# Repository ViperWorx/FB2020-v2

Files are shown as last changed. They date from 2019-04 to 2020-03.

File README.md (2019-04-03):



This is a complete re-work of our [FB2020 CoreXY](https://github.com/AxMod3DPrint/FB2020) design that fixes any faults that we have noticed over the 3 years we have had these in service in our farm. 

The Changes are listed below, this is by no means a full changelog, but the main changes are listed below:-

Major Changes v2
-----------------

* Belt Alignment - Belts were not in line, motors moved to back of printer.
* All parts redesigned or re-modelled  
* XY Gantry now underslung, due to this Z height is reduced to 120mm. This may change in a future iteration.
* Now Clad on three sides with 3mm Acrylic (Perspex). 
* Electronics now changed to MKS Gen L
* Heated bed changed to Mains Voltage heater and Aluminum Plate
* Due to the above 2 Solid State relays are needed one for PS_ON (optional) and one for the Bed (Manditory)
* Bed Long extrusions changed to 220mm to centralise the bed.
* Bed now has an 6mm Acyrilic or 2mm Aluminum (preferred) laser cut base plate to improve stability and improve ease of levelling.
* Due to the above Z Axis Bed mounting printed parts have had the levelling removed. 
* Z Lead Screw alignment fixed
* Alignment printed tools for Y & Z added. (Can be permanently mounted)
* PEI now recommended build surface. 
* Recommended firmware is now [Klipper](https://github.com/KevinOConnor/klipper)

Reliability, Speed, Accuracy, Open Source
-----------------------------------------

This sums up the FB2020 CoreXY 3D Printer. We use these printers ourselves and wouldn’t sell the kits if we didn’t think they were up to snuff. Our FB2020s have run thousands of hours with very little down time. We print all the FB2020 printed parts on our FB2020s.

Speed & Reliability
-------------------

The FB2020’s heart is the MKS GEN L running the Klipper Firmware. Klipper runs from a Raspberry Pi and offloads all calculations to the Pi. This means the FB2020 is even faster than the v1. It has tried and trusted A4988 Stepper Drivers moving the motors, which can be upgraded to Trinamic TMC 2130 for super quiet operation. With an AxMod 3D Print Drakon Geared extruder powering the filament through the bowden tube into a Genuine E3D v6 Hot end. This makes for a winning combination. The heated bed is a mains voltage heater bonded to Tool Grade 5mm Aluminium Plate which means you can print any material you wan.

Low Maintenance Accuracy
------------------------

Running the E3D v6 and the Drakon Geared Extruder, it’s smooth printing. The FB2020 is capable of layer heights of 60 Microns up to 500 Microns and can print pretty much any filament you can throw at it. 

The Bill of Materials and further infomation can be found in the Wiki.

---

<table border="0px">
<th align="left">
&copy; AxMod 3D Print 2019.
</th>
<tr>
<td>
This documentation describes Open Hardware and is licensed under the CERN OHL v. 1.2.
</td>
</tr>
<tr>
<td>
You may redistribute and modify this documentation under the terms of the
CERN OHL v.1.2. (http://ohwr.org/cernohl). This documentation is distributed
WITHOUT ANY EXPRESS OR IMPLIED WARRANTY, INCLUDING OF
MERCHANTABILITY, SATISFACTORY QUALITY AND FITNESS FOR A
PARTICULAR PURPOSE. Please see the CERN OHL v.1.2 for applicable
conditions
</td>

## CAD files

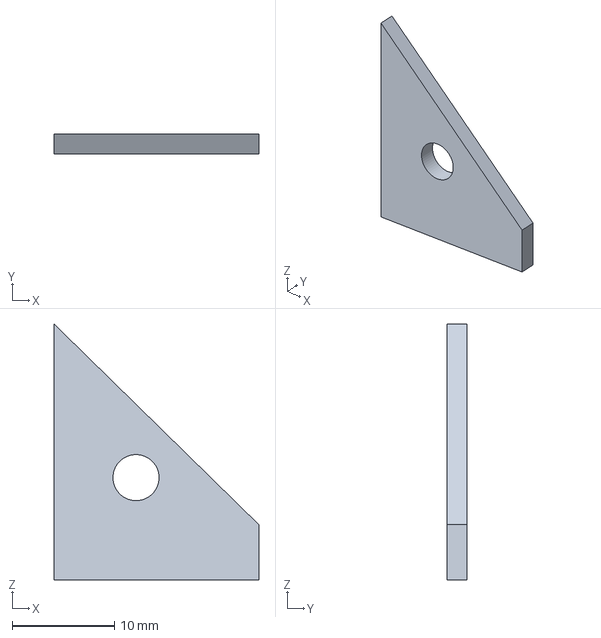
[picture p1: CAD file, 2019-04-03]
Alignment Tools/Y Alignment Tool Front.stp
20.0 x 2.00 x 25.0 mm

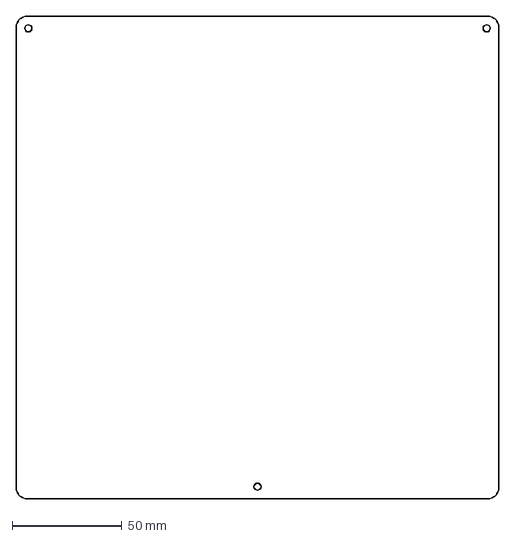
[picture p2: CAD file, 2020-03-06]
DXF/1 no Bed Plate.dxf
220.0 x 220.0 mm

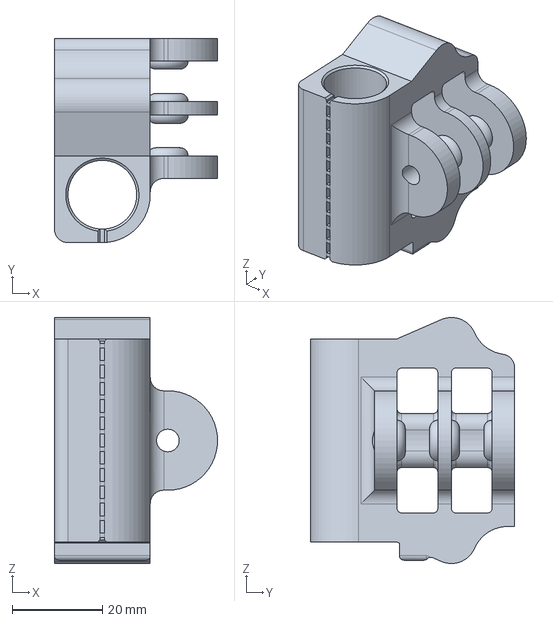
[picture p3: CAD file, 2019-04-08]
STEP/Y Carrier.stp
36.1 x 45.2 x 54.4 mm

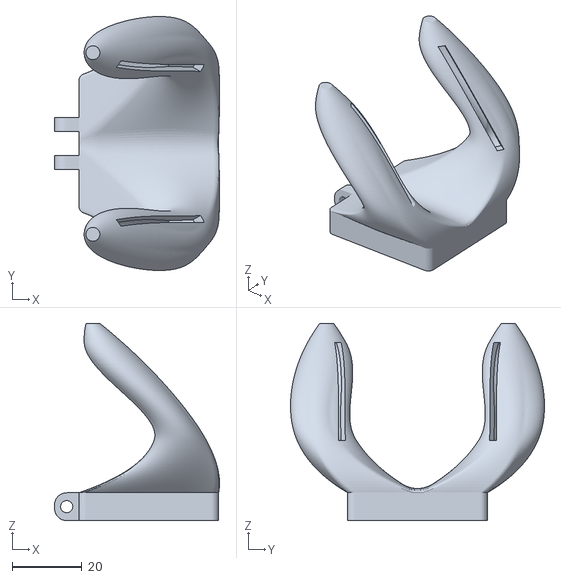
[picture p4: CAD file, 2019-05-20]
STL/1no Layer Fan Duct.stl
47.3 x 72.7 x 56.5

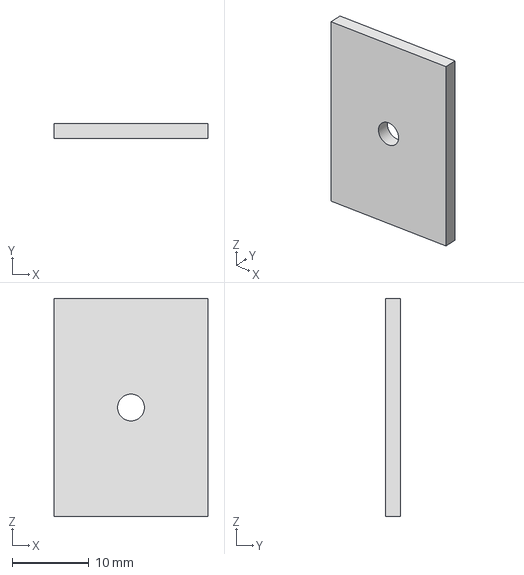
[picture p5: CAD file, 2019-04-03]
Alignment Tools/Y Alignment Tool Back.stp
20.0 x 2.00 x 28.4 mm

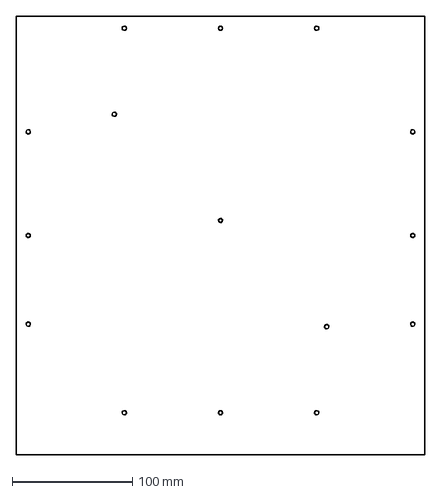
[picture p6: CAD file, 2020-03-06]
DXF/1no Side.dxf
340.0 x 365.0 mm

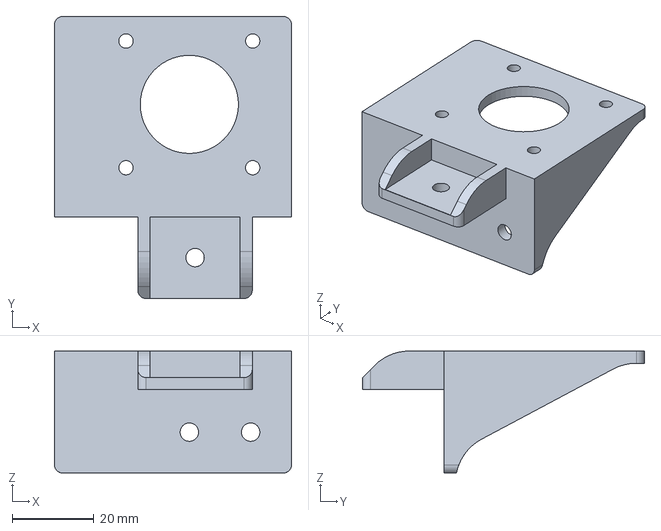
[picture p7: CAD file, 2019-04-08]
STEP/Motor Bracket Right.stp
58.0 x 69.0 x 29.9 mm

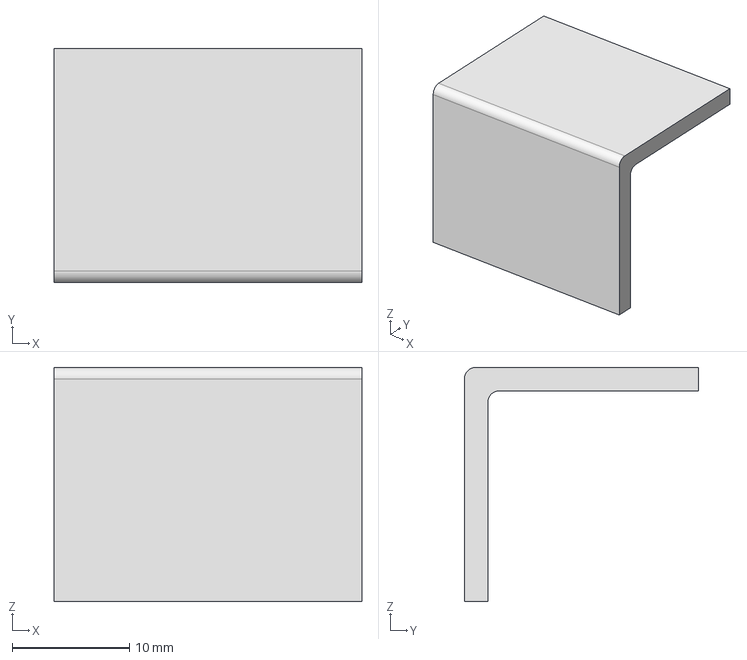
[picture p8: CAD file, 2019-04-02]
Alignment Tools/Z Motor Spacer Bottom.stp
26.3 x 20.0 x 20.0 mm

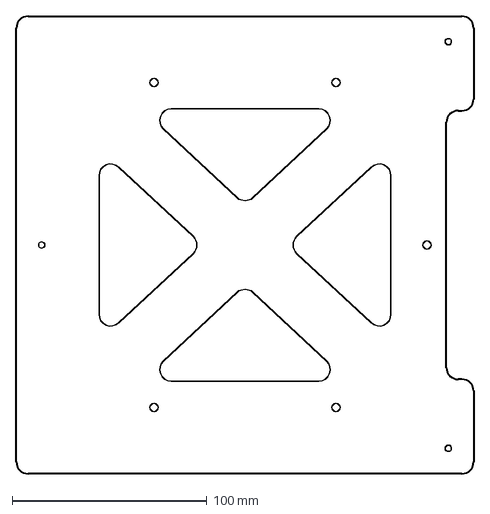
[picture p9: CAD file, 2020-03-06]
DXF/1no Bed Base Plate.dxf
235.0 x 235.0 mm

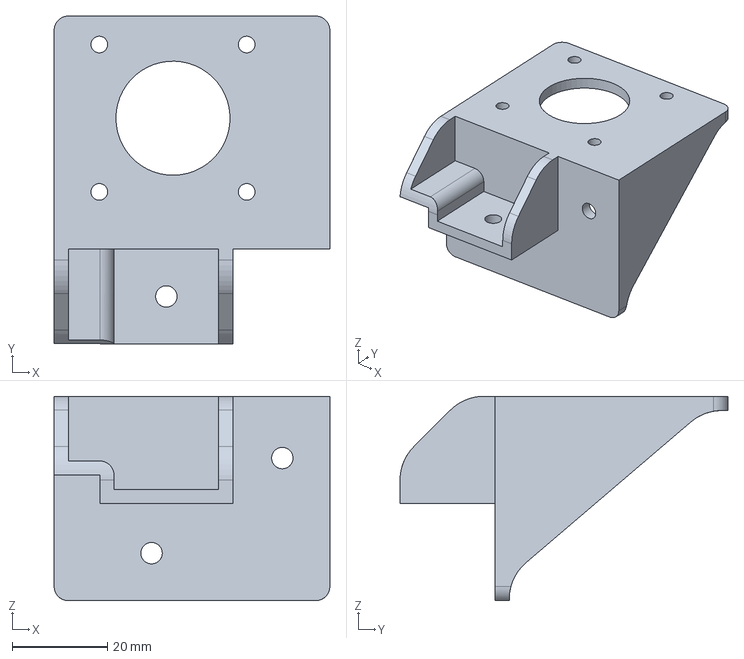
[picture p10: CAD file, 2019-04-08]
STEP/Motor Bracket Left.stp
58.0 x 69.0 x 43.0 mm

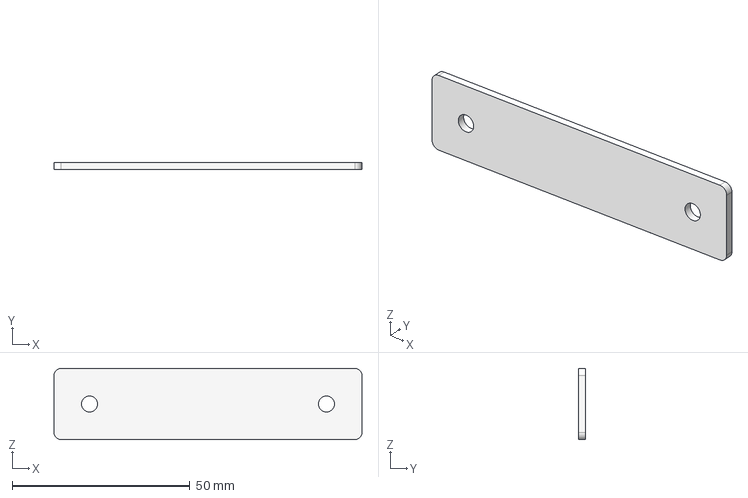
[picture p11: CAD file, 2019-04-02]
Alignment Tools/Z Axis Spacer.stp
86.7 x 2.00 x 20.0 mm

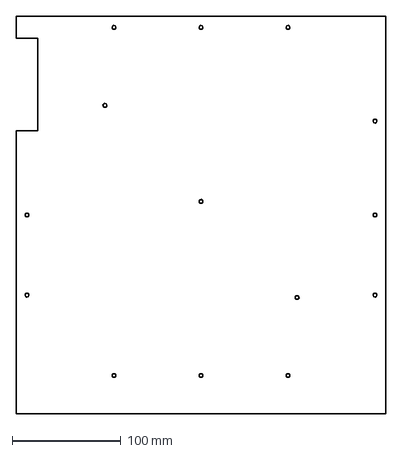
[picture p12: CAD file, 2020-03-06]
DXF/1no Side Cut - Extruder.dxf
340.0 x 365.0 mm

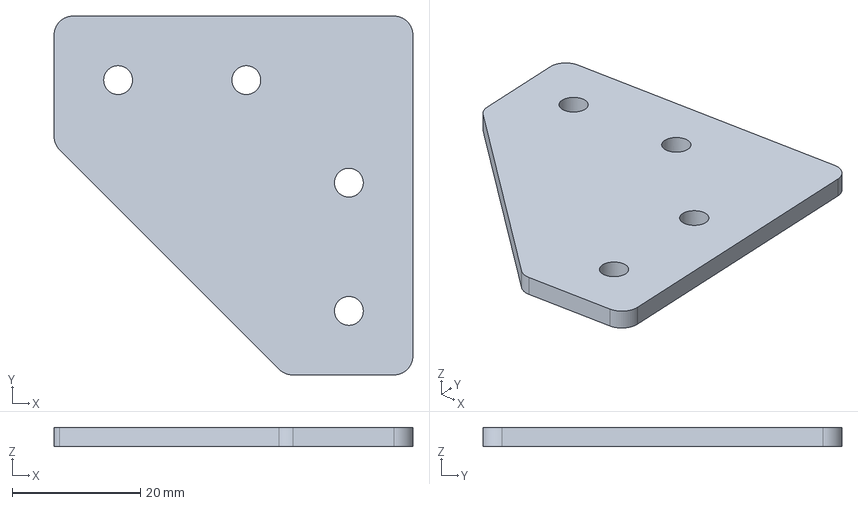
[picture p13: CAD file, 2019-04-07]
STEP/Front Top Corner Bracket.stp
56.0 x 56.0 x 3.00 mm

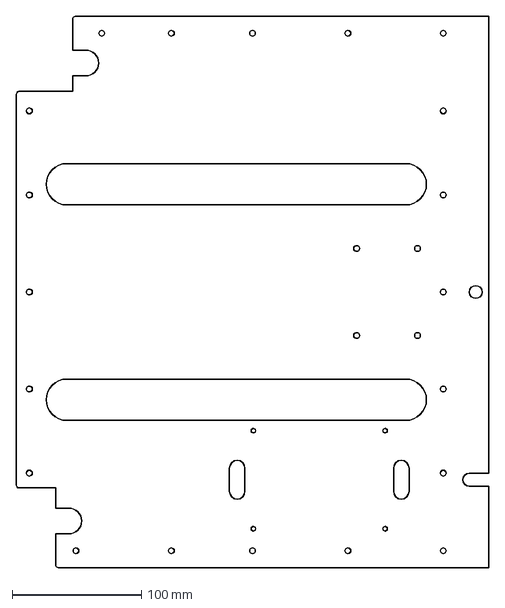
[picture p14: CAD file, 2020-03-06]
DXF/1no Back Acrylic.dxf
365.0 x 426.0 mm

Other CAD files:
STL/2no Y Carrier.stl
STL/1no Motor Bracket Right.stl
STL/1no Motor Bracket Left.stl
Alignment Tools/Z Axis Spacer Bottom.stl
Alignment Tools/Y Alignment Tool Back.stl
Alignment Tools/Y Alignment Tool Front.stl
Alignment Tools/Z Motor Spacer Bottom.stl
STEP/1no Z Motor Holder.stp
STEP/Bed Carrier Left.stp
STEP/Bed Carrier Right.stp
STEP/Carriage.stp
STEP/Corner Brace.stp
STEP/Corner Bracket.stp
STEP/Front Corner Bracket.stp
STEP/Idler Left.stp
STEP/Idler Right.stp
STEP/Layer Fan Duct.stp
STEP/Spool Holder.stp
STEP/Y Endstop Holder.stp
STEP/Y Rod Holder v2.stp
STEP/Z Endstop Mount.stp
STEP/Z Leadscrew Nut Mount.stp
STEP/Z Rod Holder.stp
STL/10no Corner Bracket.stl
STL/1no Bed Carrier Left.stl
STL/1no Bed Carrier Right.stl
STL/1no Carriage Clamp.stl
STL/1no Carriage.stl
STL/1no Idler Left.stl
STL/1no Idler Right.stl
STL/1no RRD Case Back.stl
STL/1no RRD Case Button.stl
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

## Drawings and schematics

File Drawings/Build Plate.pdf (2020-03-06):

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

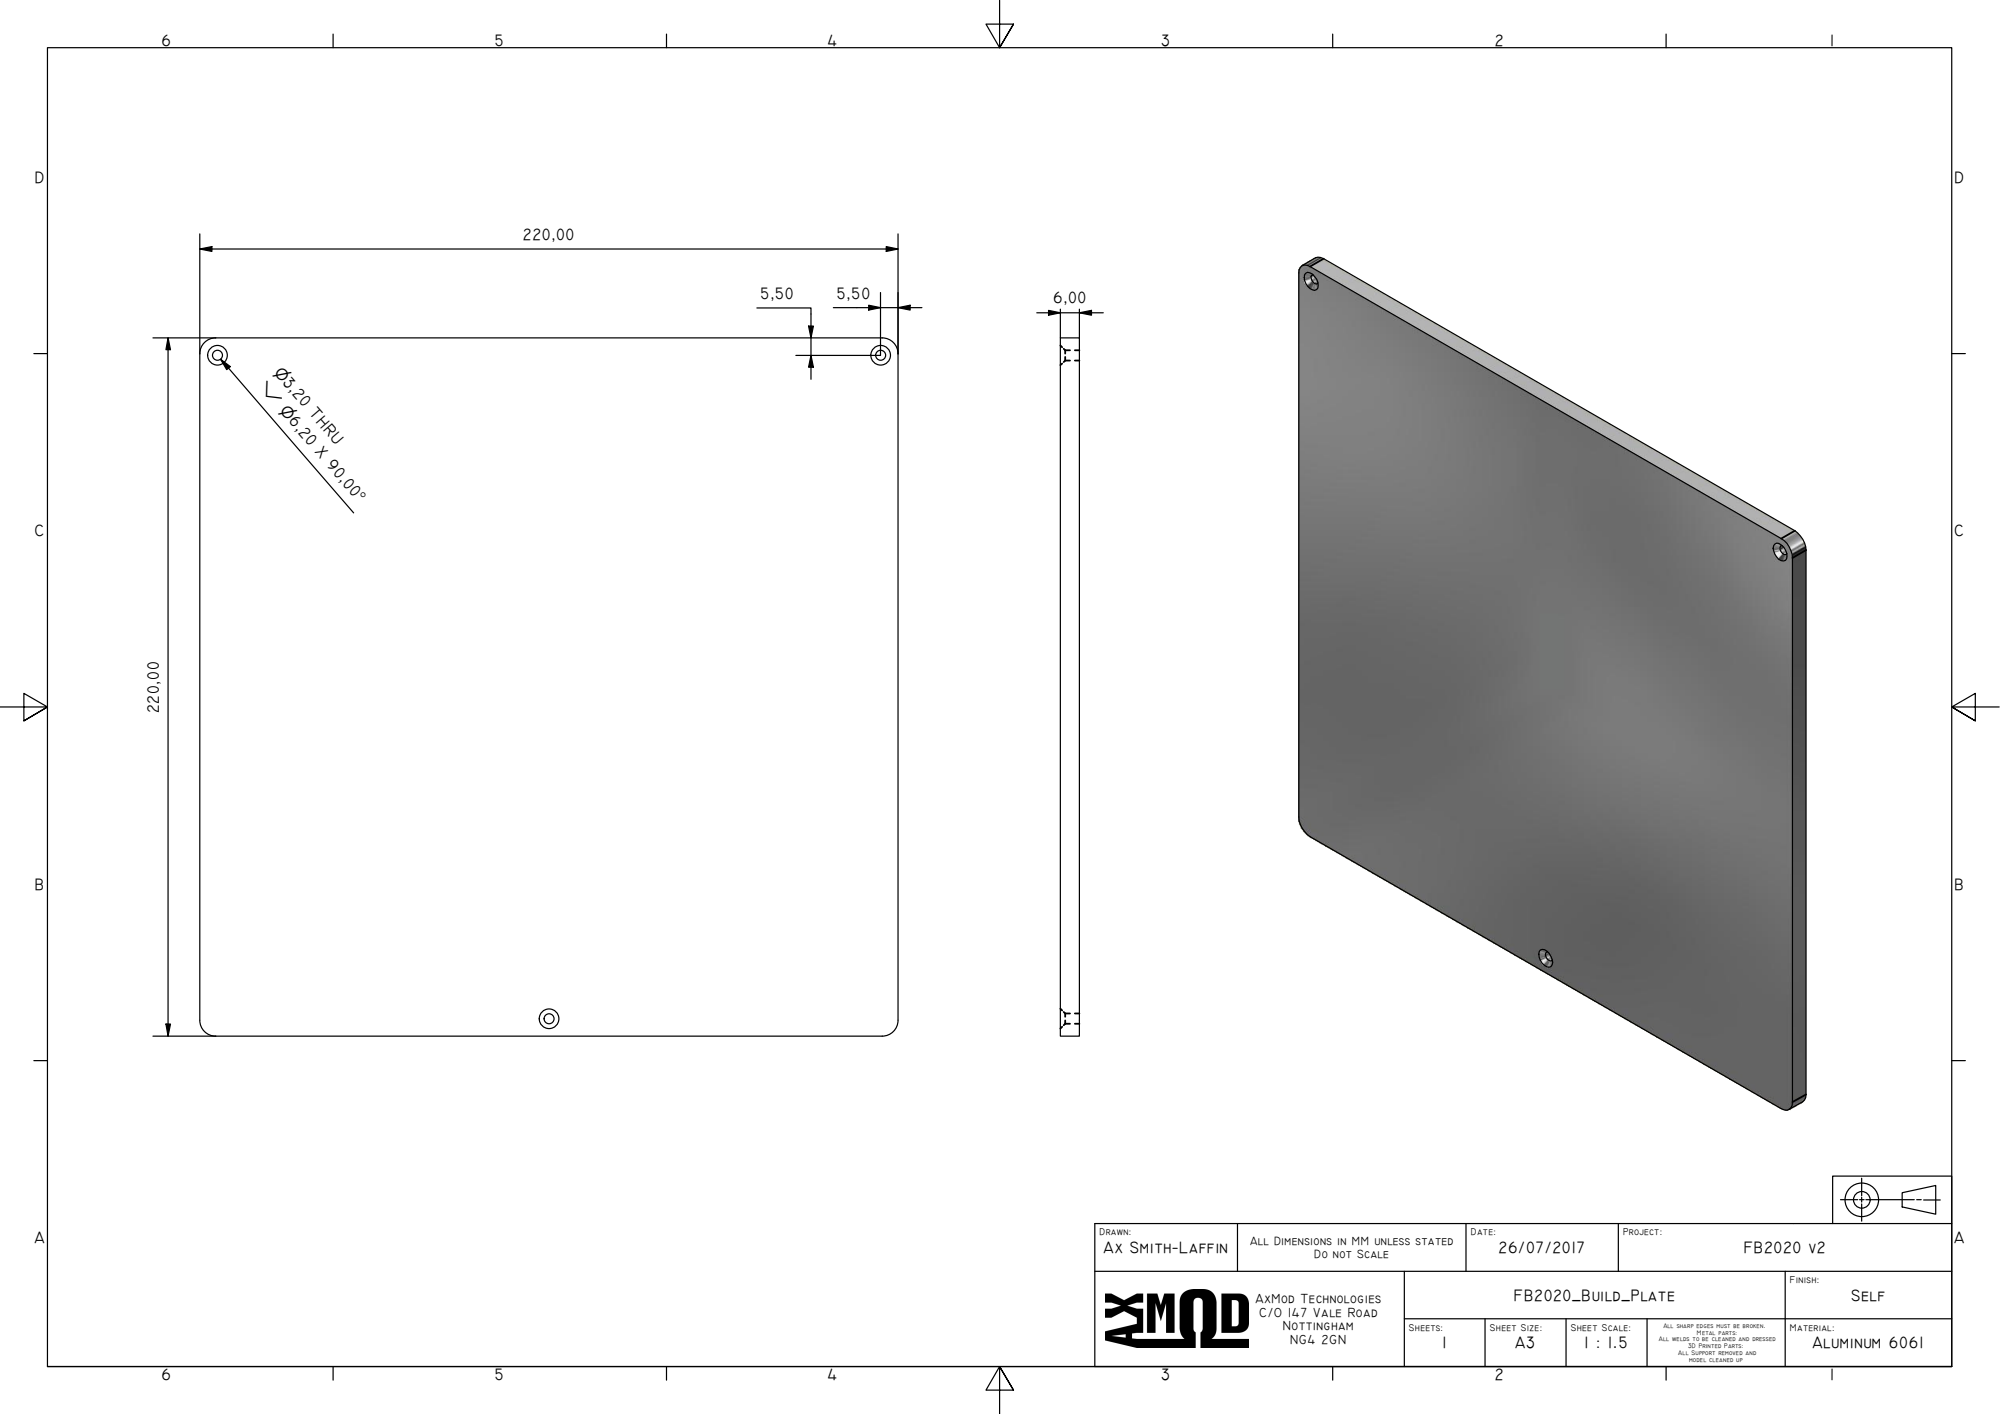
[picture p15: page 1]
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

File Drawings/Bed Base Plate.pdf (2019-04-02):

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

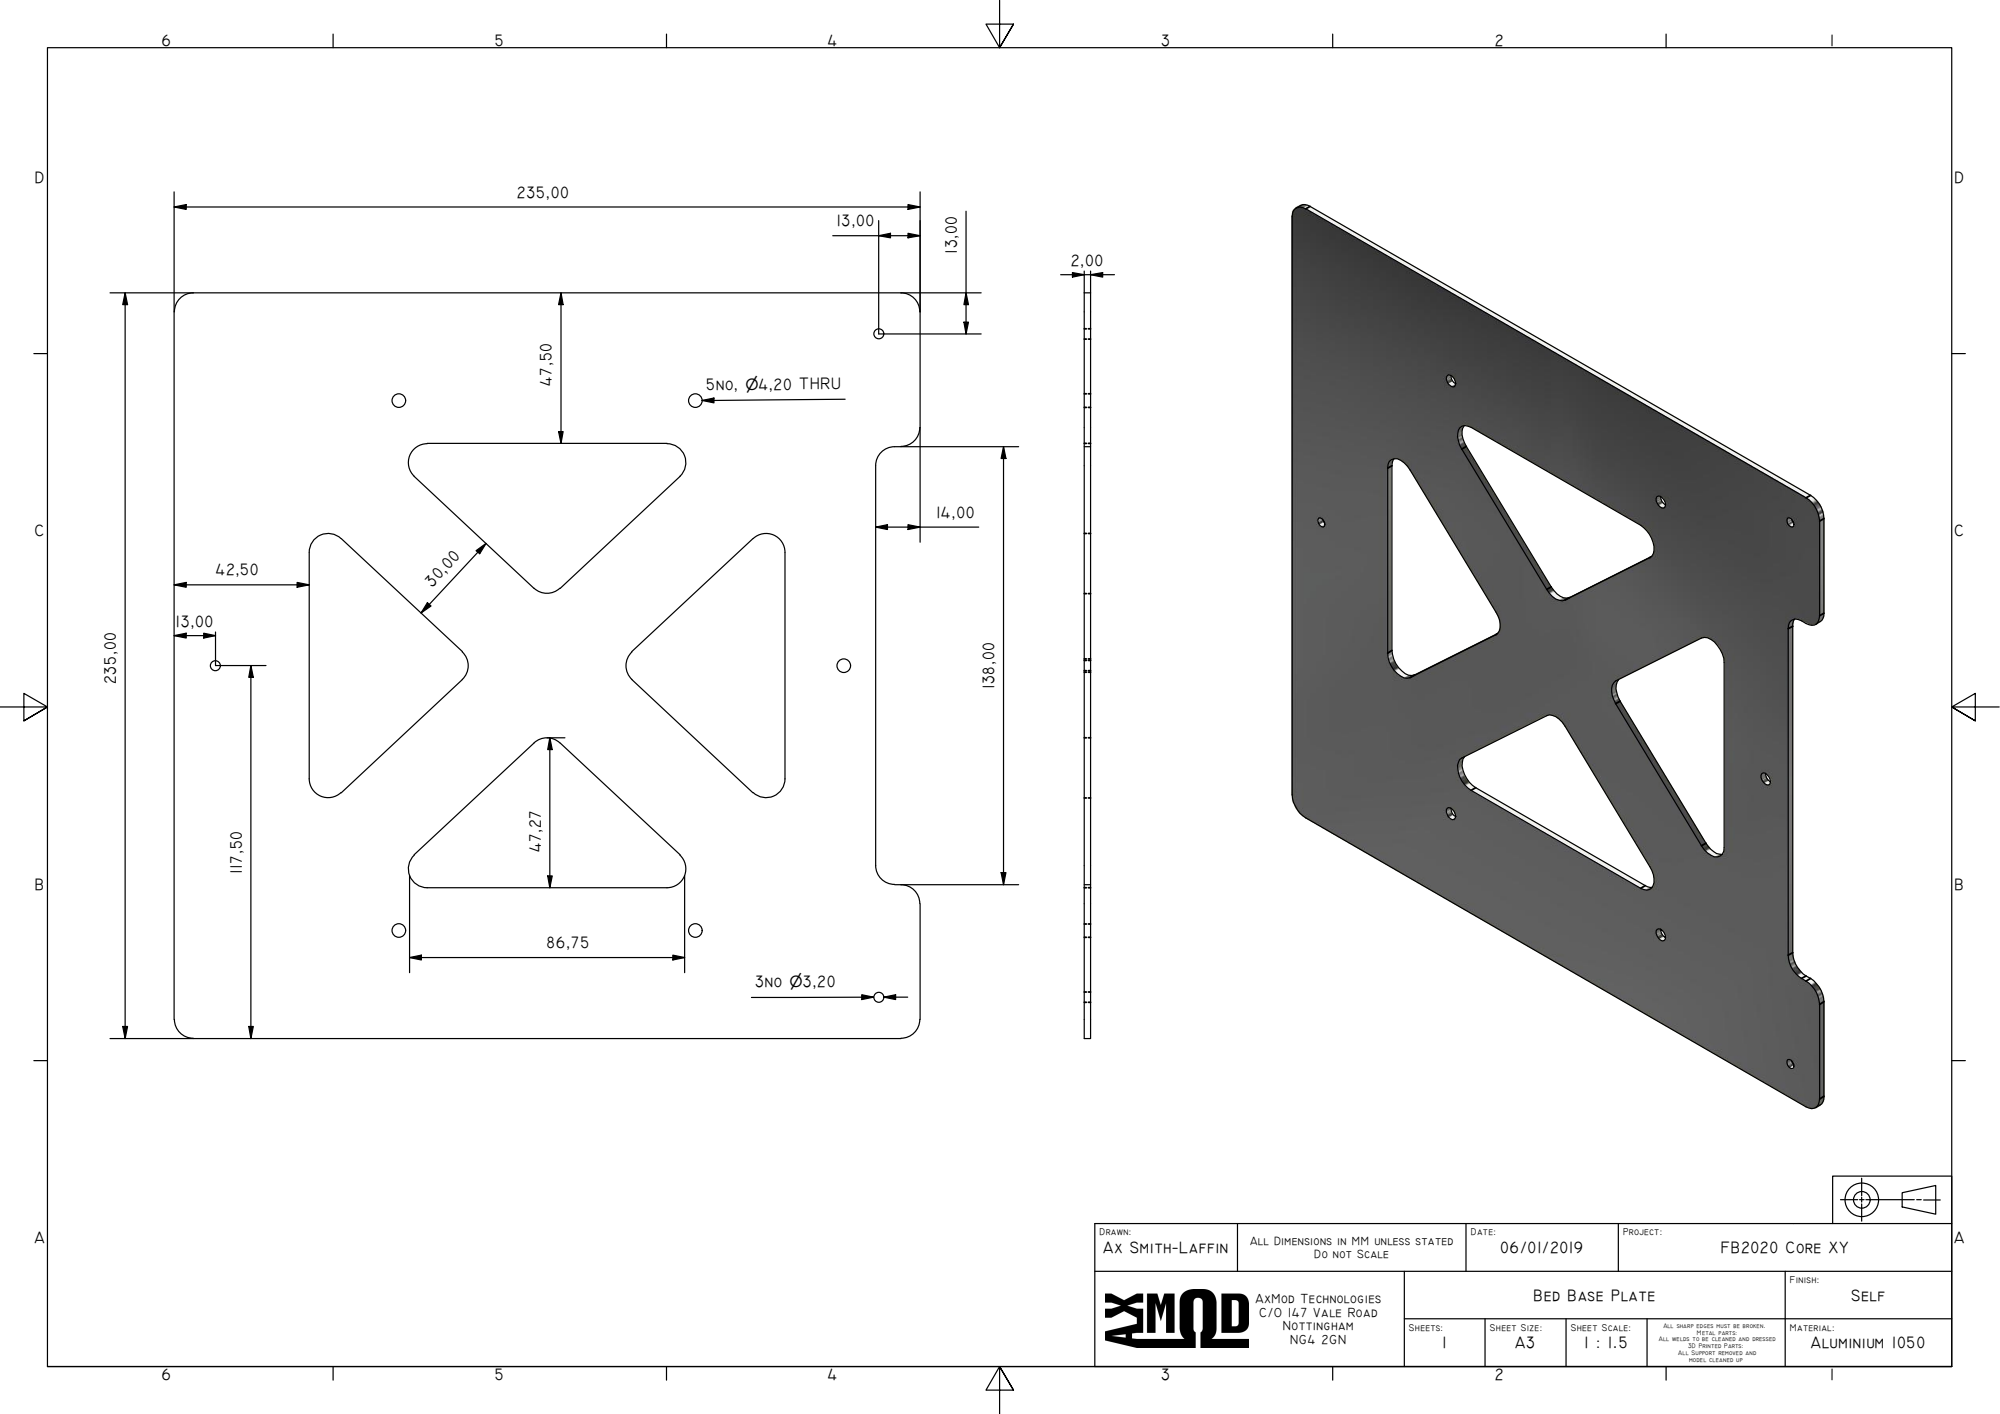
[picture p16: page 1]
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

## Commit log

2019-04-02 Initial Commit of Files
    [1 no Bed Plate.dxf, 1 no Motor Bracket Right.stl, 10no Corner Bracket.stl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]
2019-04-02 Move file to correct folder
    [4no Corner Brace.stl]
2019-04-03 Add Layer Fan Duct - Missed in initial commit
    [1no Layer Fan Duct.stl, Layer Fan Duct.stp]
2019-04-03 Add missing Alignment Tools
    [Y Alignment Tool Back.stl, Y Alignment Tool Back.stp, Y Alignment Tool Front.stl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]
2019-04-03 Change in File
    [1no Motor Bracket Right.stl, 1no Y Endstop Mount.stl]
2019-04-03 Add STLs for LCD from v1
    [1no RRD Case Back.stl, 1no RRD Case Button.stl, 1no RRD Case Front.stl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]
2019-04-06 Correct Alignment between motors and carriers
    [1no Idler Left.stl, 1no Idler Right.stl, 2no Y Carrier.stl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]
2019-04-06 Shave 0.5mm off bottom of carriage clamp - adding tolerance
    [1no Carriage Clamp.stl, Carriage.stp]
2019-04-07 Correct orientation
    [4no Y Rod Holder.stl]
2019-04-07 Reduce clamping hole to 1 only
    [4no Y Rod Holder.stl]
2019-04-07 Add Venturi fins to layer fan duct
    [1no Layer Fan Duct.stl, Layer Fan Duct.stp]
2019-04-07 Extra Fillets on fan duct
    [1no Layer Fan Duct.stl, Layer Fan Duct.stp]
2019-04-07 Motor bracket flexing - gusset added to stop
    [1no Motor Bracket Left.stl, 1no Motor Bracket Right.stl, Motor Bracket Left.stp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]
2019-04-07 Remove Z Axis Top spacer - no longer required
    [Z Axis Spacer Top.stl, Z Axis Spacer Top.stp]
2019-04-07 Z Endstop Mount - adjust hole sizes
    [1no Z Endstop Mount Clamp.stl, 1no Z Endstop Mount.stl, Z Endstop Mount.stp]
2019-04-07 Add front top corner bracket - added strength and alignment
    [2no Front Top Corner Bracket.stl, Front Top Corner Bracket.stp]
2019-04-08 Add clearance for motor
    [1no Motor Bracket Left.stl, 1no Motor Bracket Right.stl, Motor Bracket Left.stp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]
2019-04-08 Add extra clearance for smooth rods
    [2no Y Carrier.stl, Y Carrier.stp]
2019-05-20 Update Layer fan Duct - full redesign
    [1no Layer Fan Duct.stl]
2020-03-06 Update DXF files - Old versions uploaded
    [1 no Bed Plate.dxf, 1no Back Acrylic.dxf, 1no Bed Base Plate.dxf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]
2020-03-06 Update Build Plate Drawing
